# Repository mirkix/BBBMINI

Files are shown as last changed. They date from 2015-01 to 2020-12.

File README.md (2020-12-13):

# BBBmini

BeagleBone Black / Green  (BBB / BBG) Linux ArduPilot DIY Cape

(https://youtu.be/SqyfN3FStvs)

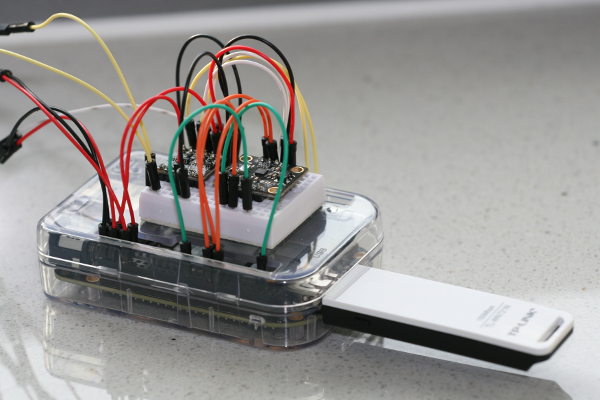
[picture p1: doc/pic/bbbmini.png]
BBBMINI breadboard


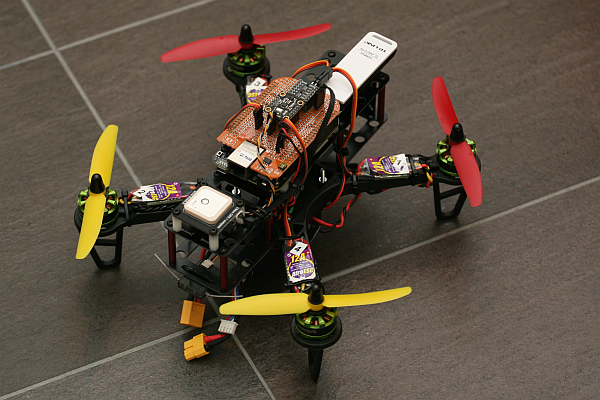
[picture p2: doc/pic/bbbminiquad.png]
BBBMINI Quad


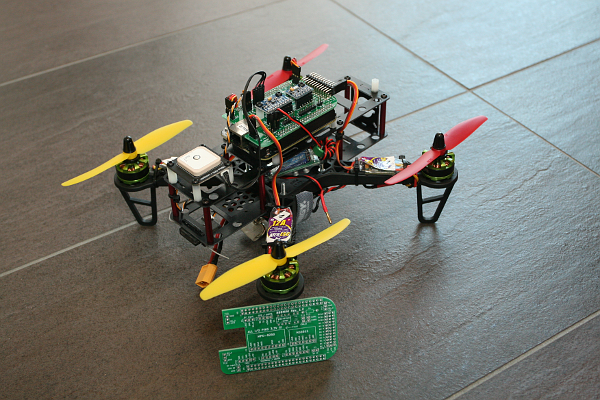
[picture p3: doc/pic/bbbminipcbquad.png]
BBBMINI Quad


# Why?
* Have fun to build your own BeagleBone ArduPilot Cape
* Easy start to ArduPilot Linux development
* No SMD soldering required
* DIY friendly connector

# About BBBmini
BBBmini is an autopilot / flightcontroller Cape for the BeagleBone. BBBmini + BeagleBone can be used as a state of the art Linux autopilot / flightcontroller for Copter, Planes or Rovers. BBBmini can be used with ArduPilot (open source unmanned aerial vehicle flight stack. BBBmini is a DIY project using widely available IMU and barometer breakout sensor boards, there is no SMD soldering necessary. The design is made that everybody can build a BBBmini by himself. In flight internet connection is done via WiFi link.

What does BBBmini offer:

* DIY state of the art UAV autopilot / flightcontroller
* Easy to build, no SMD soldering necessary
* Free hardware, free software
* Autopilot / flightcontroller software is running on Real-Time Linux
* DIY friendly connectors 0.1” pin header
* 12 x PWM out with individual frequency for each channel
* RC in connector for PPM, S.BUS or spektrum satellite input
* MPU-9250 IMU 9 x DOF
* MS5611 barometer
* HC-SR04 ultrasonic rangefinder
* GPS for full autonomous flights
* Voltage and current sensing
* I2C connector for Status display and additional sensors
* SPI connector for second redundant IMU
* UART connector for GPS
* UART connector for telemetry
* CAN connector with on board CAN bus transceiver
* USB connector used for WiFi, Laser rangefinder or cameras
* Excellent cost-performance ratio

The BBBmini project development includes:
* BBBmini documentation / how to
* BBBmini PCB design done with Kicad all sources free available on Github
* Device tree file for BBBmini hardware
* PRU firmware: 12 x PWM OUT with better than 1us accuracy, separate frequency for each channel. RC input capture with 5ns accuracy, can be used to capture PPM, S.BUS or spektrum satellite
* PRU firmware: HC-SR04 Ultrasonic Rangefinder device driver
* Commits to ArduPilot project to get BBBmini supported by ArduPilot
* Development of status display device driver for ArduPilot
* Add redundancy sensors via SPI / I2C or UART
* Lots of test flights and fine tuning in hardware and software to get a stable and reliable BeagleBone Green flightcontroller

# Why BeagleBone

Once I had the idea to develop a flightcontroller, I have examined on the market available computer for their suitability. The following criteria should be met by the computer being used.

First, the computer should be very well supported by the community. As a result, a Raspberry Pi or BeagleBone could be used. In addition, the flightcontroller should be set up with as little as possible external components.

The decision was made for the BeagleBone. With the Programmable Real-Time Units of the BeagleBone, it is possible to create the BBBmini with only a few sensor breakout boards. In addition the BeagleBone offers many interfaces such as UART, SPI, I2C, CAN, USB and ADC. All these interfaces are used by the BBBmini.

## BeagleBone parts used for BBBmini

* Main CPU running Linux
* PRU0 device driver for HC-SR04 ultrasonic rangefinder
* PRU1 to generate 12 PWM signals and receive PPM, S.BUS or spektrum satellite input
* Grove / I2C for communication to the status display, external compass or Laser rangefinder
* GROVE / serial 2 for sensors like Laser Rangefinder
* Serial 4 for telemetry radio
* Serial 5 for GPS
* ADC for voltage and current sensing
* SPI1 for high speed data transfer from IMU and Baro sensor
* SPI0 for high speed data transfer from second redundant IMU or other hardware
* CAN for communication with ESCs and additional hardware
* USB for WiFi and camera connection for life HD video transmission
* Ethernet for communication on ground

# [Hardware](doc/hardware/hardware.md)
* [BeagleBone Black](https://beagleboard.org/black) or [BeagleBone Green](https://beagleboard.org/green)
* [BBBMINI-PCB](https://github.com/mirkix/BBBMINI-PCB) (recommended) or BeagleBone Proto Cape with IMU MPU-9250 breakout board and Baro MS5611 breakout board (try to get a GY-9250 and GY-63 breakout board)
* RC receiver (S.BUS, PPM-Sum, Spektrum Satellit SPM 9645)
* optional GPS receiver
* optional HC-SR04 Ultrasonic Module

Click [here](doc/hardware/hardware.md) for further instruction how to assemble the board.

# [Software](doc/software/software.md)
For instructions how to get, build, test and run the software click [here](doc/software/software.md).

# Hackster.io
Please check also my [BBBmini project description on hackster.io](https://www.hackster.io/mirkix/flying-beaglebone-green-448b60).

# Support

## Support Chat



## Forum

[ArduPilot Forum](http://discuss.ardupilot.org/c/hardware-discussion/linux-autopilots)

## User Group

[diydrones.com BBBmini User Group](http://diydrones.com/group/bbbmini)

# License

<br /><span xmlns:dct="http://purl.org/dc/terms/" property="dct:title">BBBmini</span> by <a xmlns:cc="http://creativecommons.org/ns#" href="https://github.com/mirkix" property="cc:attributionName" rel="cc:attributionURL">Mirko Denecke</a> is licensed under a <a rel="license" href="http://creativecommons.org/licenses/by-sa/4.0/">Creative Commons Attribution-ShareAlike 4.0 International License</a>.

UNLESS OTHERWISE MUTUALLY AGREED TO BY THE PARTIES IN WRITING, LICENSOR OFFERS THE WORK AS-IS AND MAKES NO REPRESENTATIONS OR WARRANTIES OF ANY KIND CONCERNING THE WORK, EXPRESS, IMPLIED, STATUTORY OR OTHERWISE, INCLUDING, WITHOUT LIMITATION, WARRANTIES OF TITLE, MERCHANTABILITY, FITNESS FOR A PARTICULAR PURPOSE, NONINFRINGEMENT, OR THE ABSENCE OF LATENT OR OTHER DEFECTS, ACCURACY, OR THE PRESENCE OF ABSENCE OF ERRORS, WHETHER OR NOT DISCOVERABLE. SOME JURISDICTIONS DO NOT ALLOW THE EXCLUSION OF IMPLIED WARRANTIES, SO SUCH EXCLUSION MAY NOT APPLY TO YOU. EXCEPT TO THE EXTENT REQUIRED BY APPLICABLE LAW, IN NO EVENT WILL LICENSOR BE LIABLE TO YOU ON ANY LEGAL THEORY FOR ANY SPECIAL, INCIDENTAL, CONSEQUENTIAL, PUNITIVE OR EXEMPLARY DAMAGES ARISING OUT OF THIS LICENSE OR THE USE OF THE WORK, EVEN IF LICENSOR HAS BEEN ADVISED OF THE POSSIBILITY OF SUCH DAMAGES.

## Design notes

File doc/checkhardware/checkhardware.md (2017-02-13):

# Check hardware
If your board is ready you can check that everything is working as expected.

To build the example code / test code follow the instructions below.

## Compile example / test code native on BeagleBone
1. `cd ardupilot`
2. `git checkout master`
3. `git submodule update --init --recursive`
4. `./waf configure --board=bbbmini`
5. `./waf examples` (take some time)
6. `cp build/bbbmini/examples/* /home/debian/`

## Cross compile example / test code (faster) with Ubuntu computer

1. `cd ardupilot`
2. `git checkout master`
3. `git submodule update --init --recursive`
4. `./waf configure --board=bbbmini`
5. `./waf examples`
6. `scp build/bbbmini/examples/* debian@beaglebone:/home/debian/`

## Check IMU
`sudo /home/debian/INS_generic`

## Check baro
`sudo /home/debian/BARO_generic`

## Check GPS
`sudo /home/debian/GPS_AUTO_test -B /dev/ttyO5`

## Check rcinput
`sudo /home/debian/RCInput`

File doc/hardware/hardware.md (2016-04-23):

#Hardware

## Schematic
Schematic

## PCB
PCB

## Assemble BBBmini

### Step 1: Solder resistor R4 and R5.

For 3.3V RC input signal use R4 = 0Ω (bridge) and R5 = open (see picture)

For 5V RC input signal use R4 = 1kΩ and R5 = 2kΩ

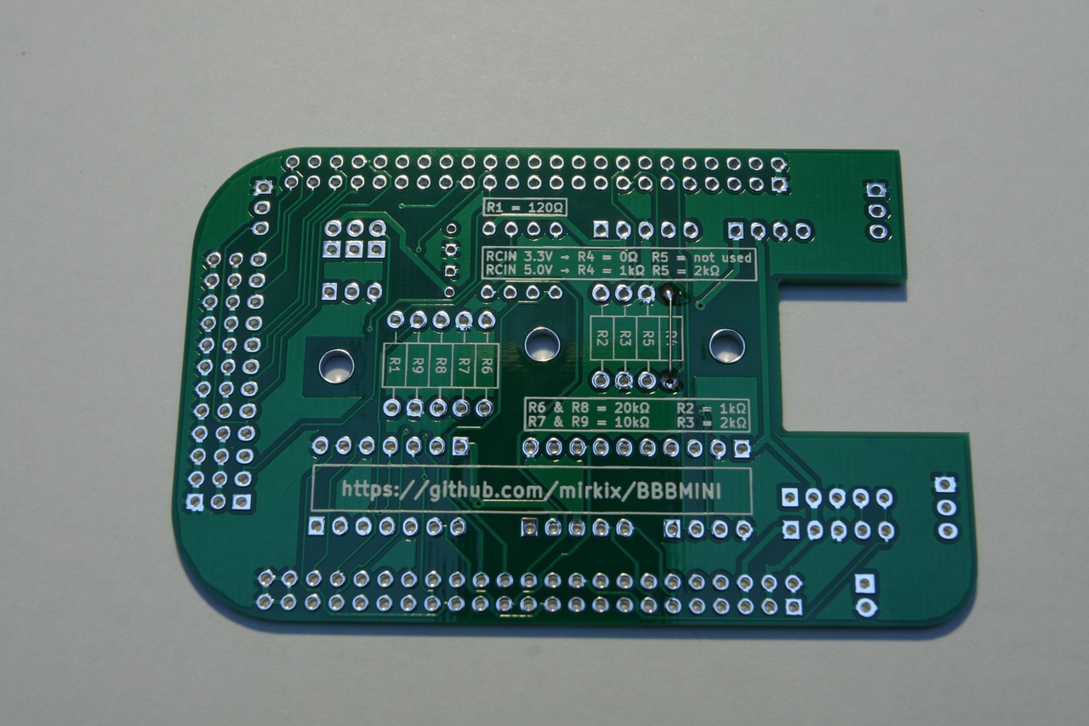
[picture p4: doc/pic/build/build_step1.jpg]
Solder R4 and R5


### Step 2:

Solder resistor

R1 = 120Ω

R2 = 1kΩ

R3 = 2kΩ

R6 = 20kΩ 0.1%

R7 = 10kΩ 0.1%

R8 = 20kΩ 0.1%

R9 = 10kΩ 0.1%

to the bottom layer. 

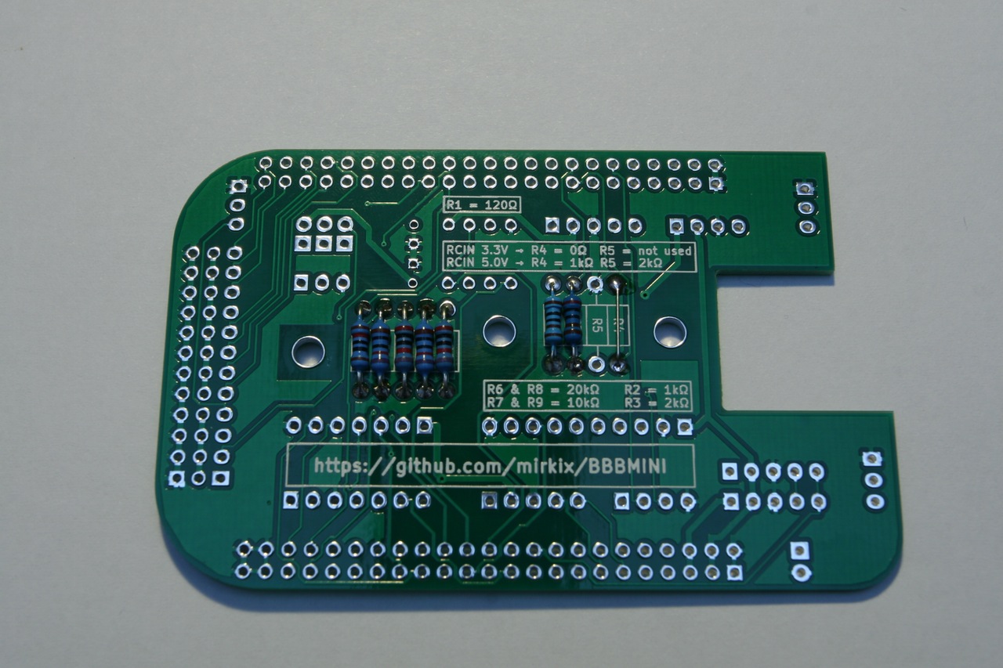
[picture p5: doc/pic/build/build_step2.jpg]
Solder R1, R2, R3, R6, R7, R8 and R9


### Step 3:

Solder CAN transceiver on the top layer

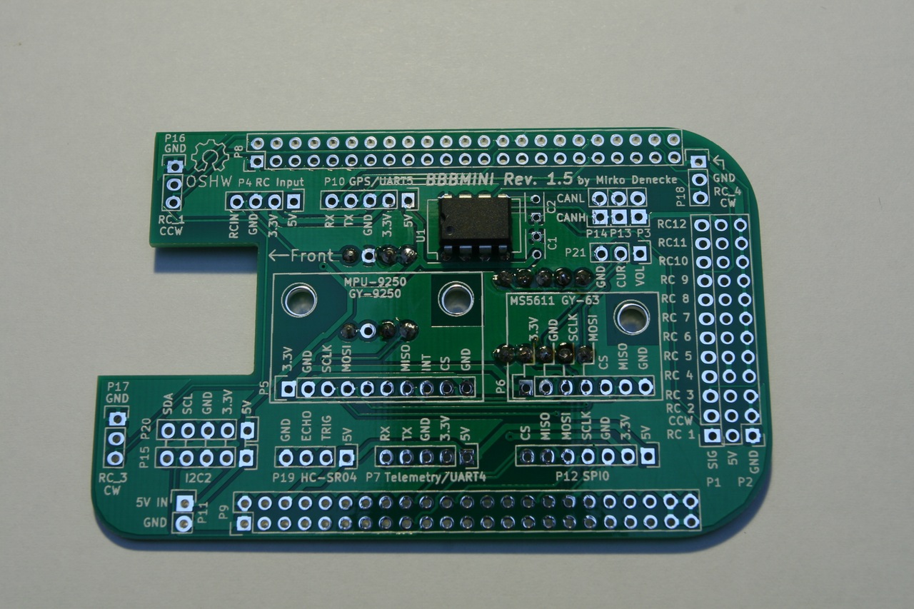
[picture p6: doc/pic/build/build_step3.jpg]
Solder CAN transceiver


### Step 4:

Solder male pin-header on top layer

P1, P2, P3, P4, P7, P10, P11, P12, P13, P14, P15, P16, P17, P18, P19, P20, P21

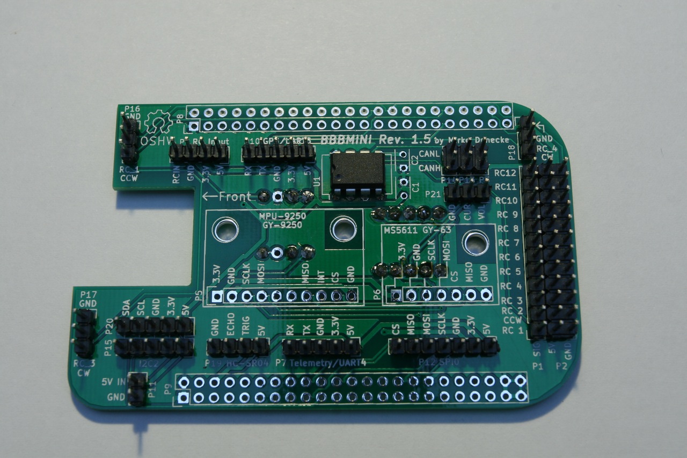
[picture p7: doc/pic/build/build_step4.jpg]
Solder P1, P2, P3, P4, P7, P10, P11, P12, P13, P14, P15, P16, P17, P18, P19, P20, P21


### Step 5:

Solder C1 and C2

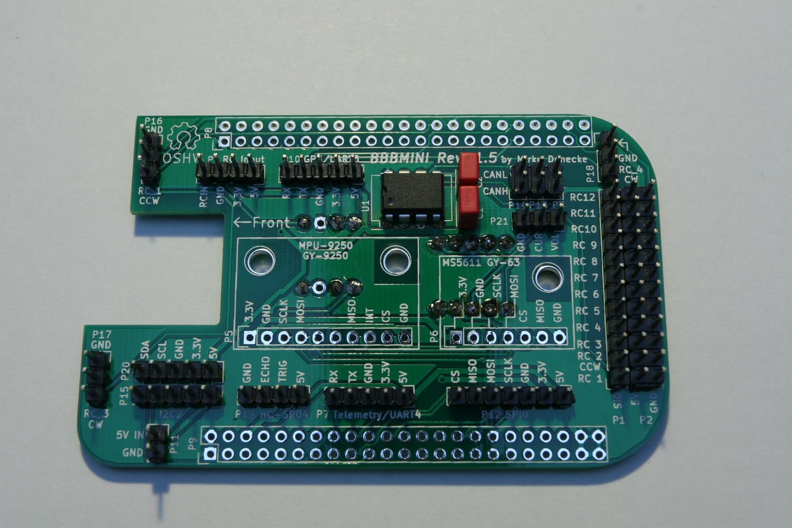
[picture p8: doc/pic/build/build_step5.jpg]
Solder C1 and C2


### Step 6:

Solder female pin-header P5 and P6 on top layer

Solder P5 and P6

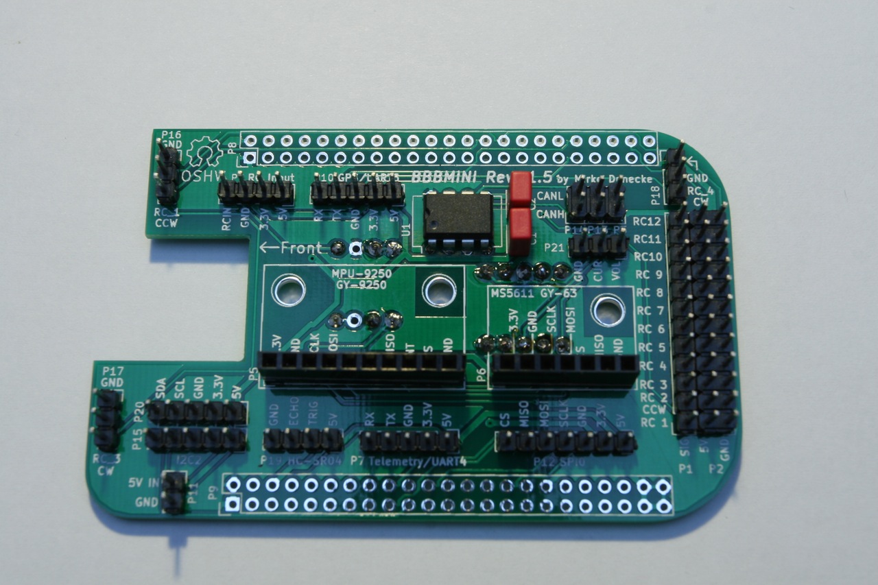
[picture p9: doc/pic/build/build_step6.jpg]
Solder P5 and P6


### Step 7:

Solder male pin-header P8 and P9 to bottom layer

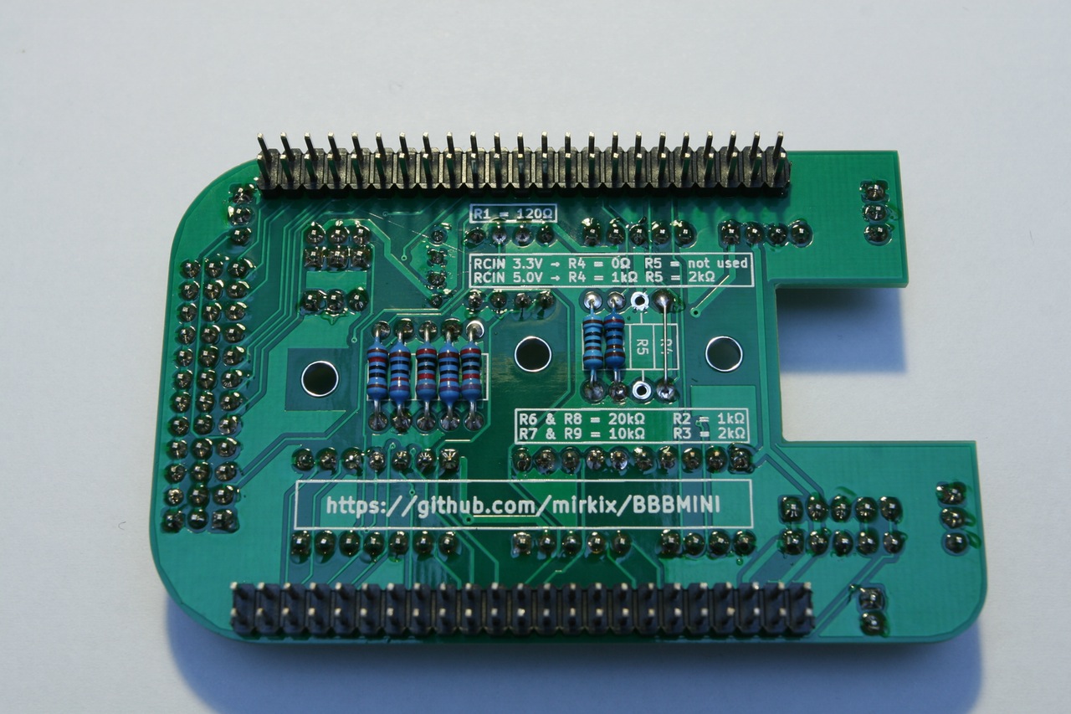
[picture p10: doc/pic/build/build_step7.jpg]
Solder P8 and P9


### Step 8:

Solder male pin-header to bottom layer of GY-9250 and GY-63

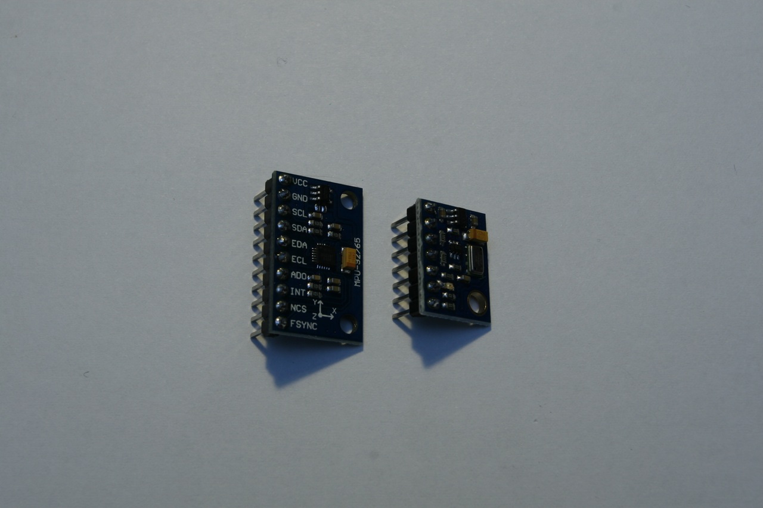
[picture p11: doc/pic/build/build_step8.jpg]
Solder pin-header for GY-9250 and GY-63


### Step 9:

Mount spacer to BBBmini

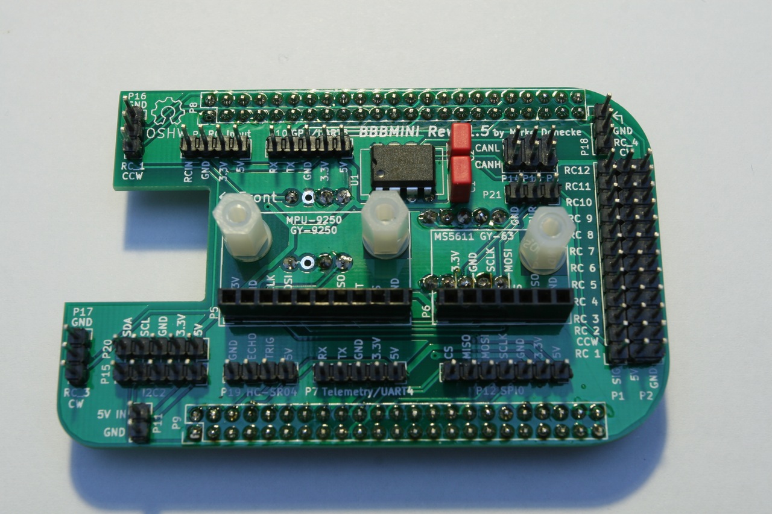
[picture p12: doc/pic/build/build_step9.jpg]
Mount spacer


### Step 10:

Mount GY-9250 and GY-63

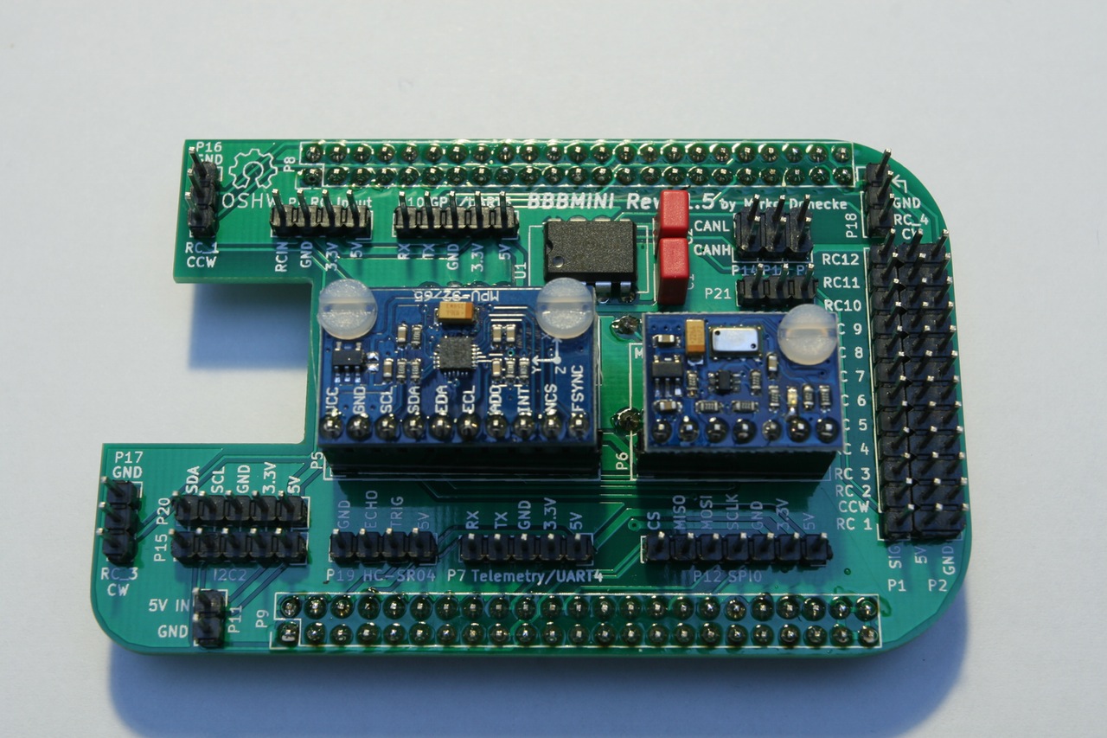
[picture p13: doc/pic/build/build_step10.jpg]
Mount GY-9250 and GY-63


### Finish! BBBmini is ready to use for Copter, Planes or Rover.

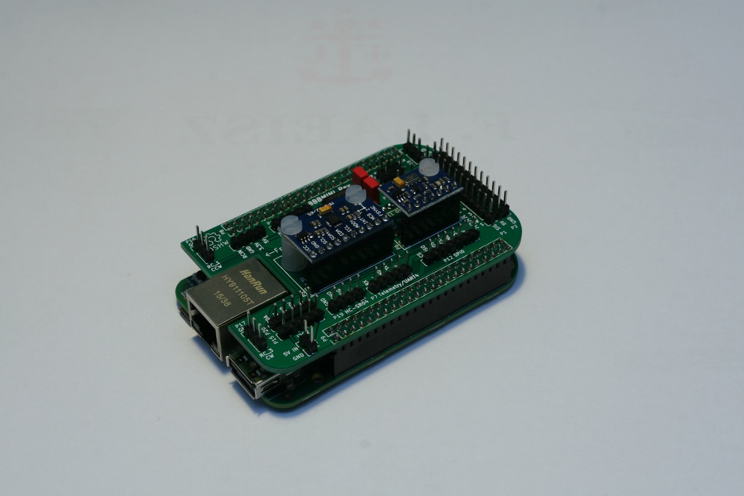
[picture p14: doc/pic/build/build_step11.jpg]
BBBmini


## Connect BBBmini

### Connect motors and ESC
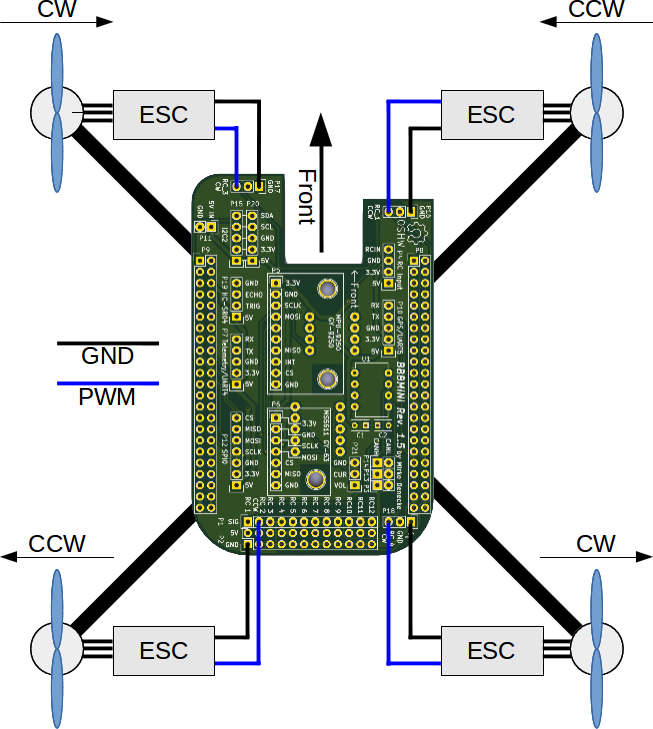
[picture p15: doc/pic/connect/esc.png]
Connect motors and ESC


### Connect power distribution

* Connect each ESC to the power distribution board
* Connect the 5V power distribution board output to BBBmini P11 power input
* Connect the voltage and current sensing power distribution board output to BBBmini P21 voltage and current sensing pins

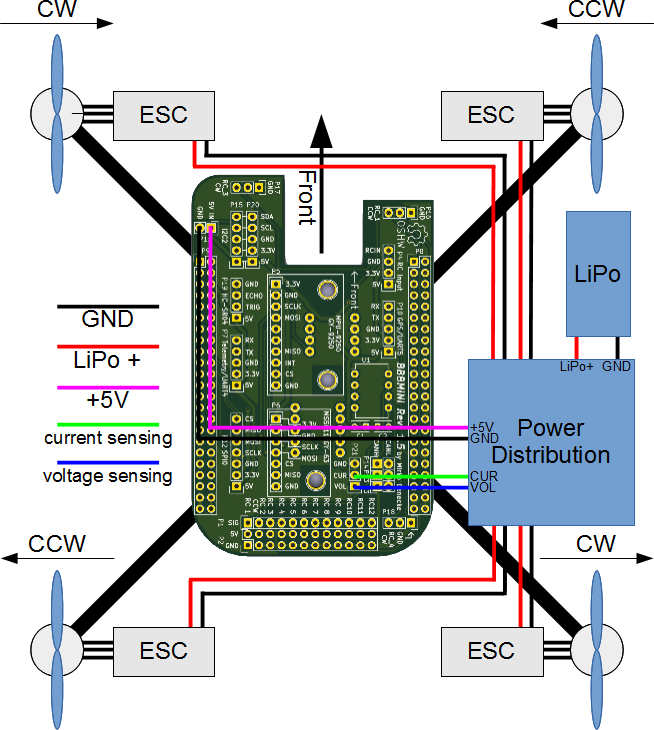
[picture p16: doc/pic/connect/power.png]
Connect power distribution


### Connect RC receiver
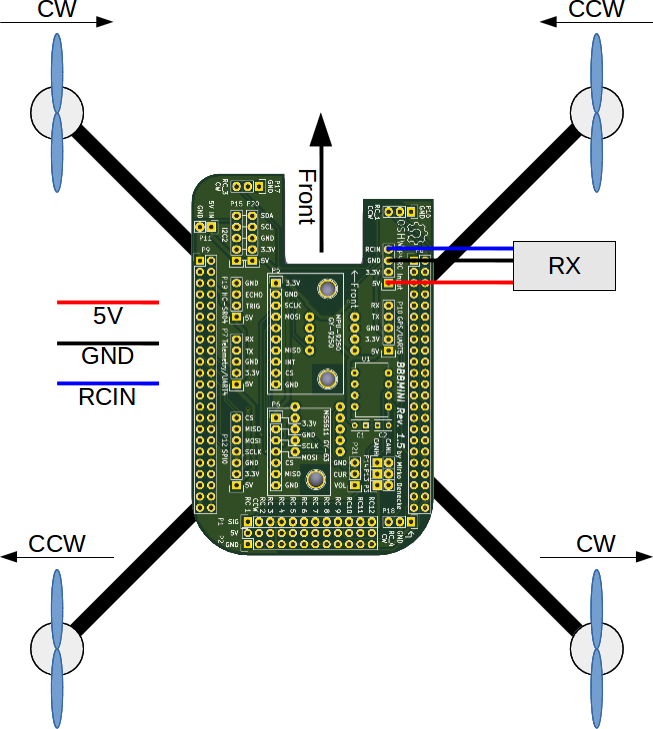
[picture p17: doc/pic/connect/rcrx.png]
Connect RC receiver


### Connect display
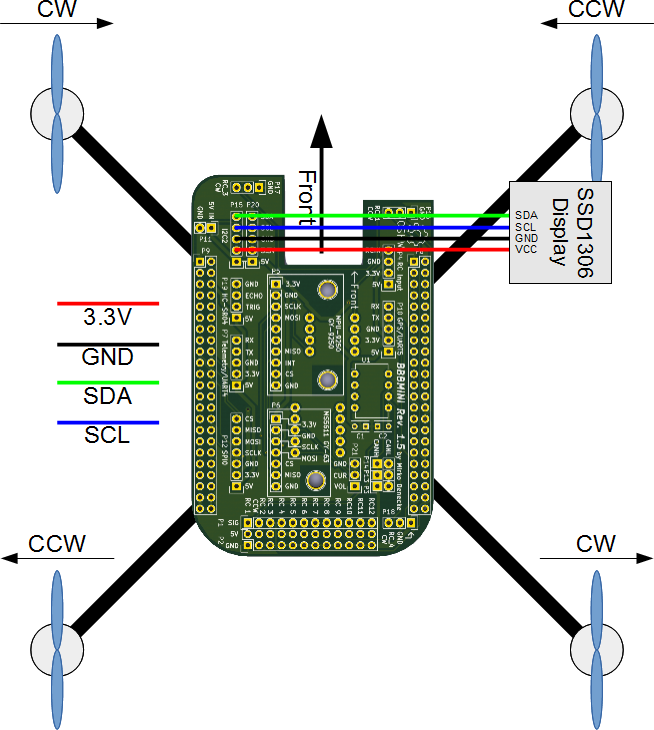
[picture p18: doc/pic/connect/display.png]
Connect display


### Connect GPS

* Connect your GPS to P10.
* P10 +3.3V to GPS VCC
* P10 GND to GPS GND
* P10 RX to GPS TX
* P10 TX to GPS RX

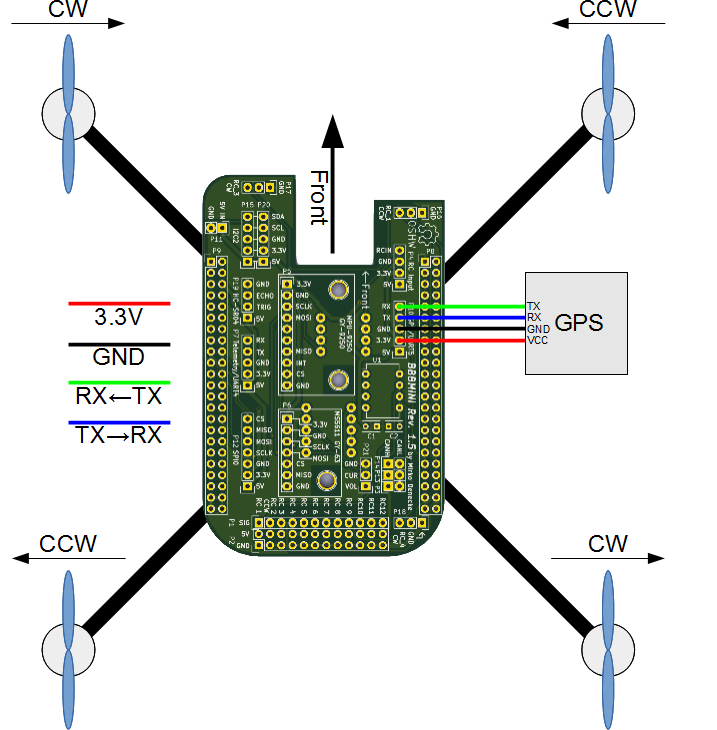
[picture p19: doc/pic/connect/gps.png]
Connect GPS


### Connect telemetry

* Connect your telemetry radio to P7.
* P7 +5V to telemetry radio VCC
* P7 GND to telemetry radio GND
* P7 RX to telemetry radio TX
* P7 TX to telemetry radio RX

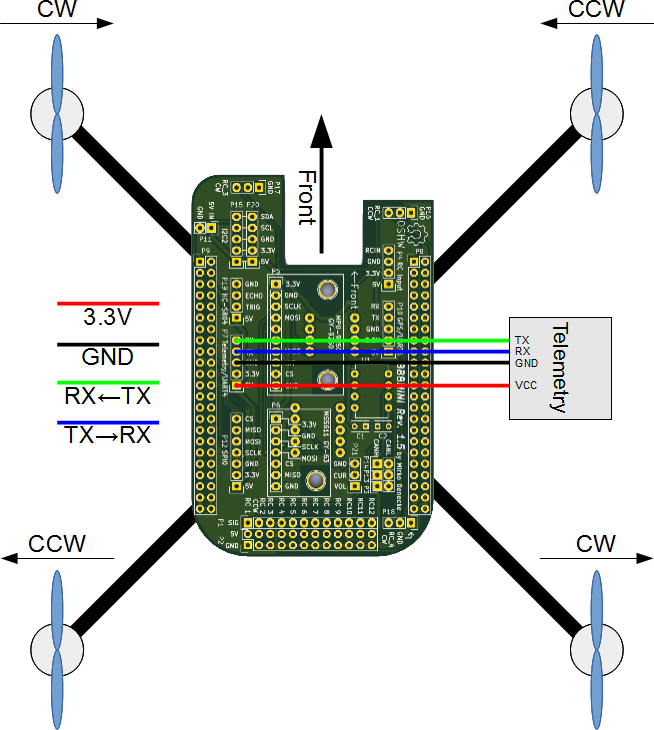
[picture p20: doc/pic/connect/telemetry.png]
Connect telemetry


### Connect HC-SR04

* Connect your HC-SR04 ultrasonic rangefinder
* P19 +5V to HC-SR04 VCC
* P19 GND to HC-SR04 GND
* P19 TRIG to HC-SR04 TRIG
* P19 ECHO to ECHO TRIG

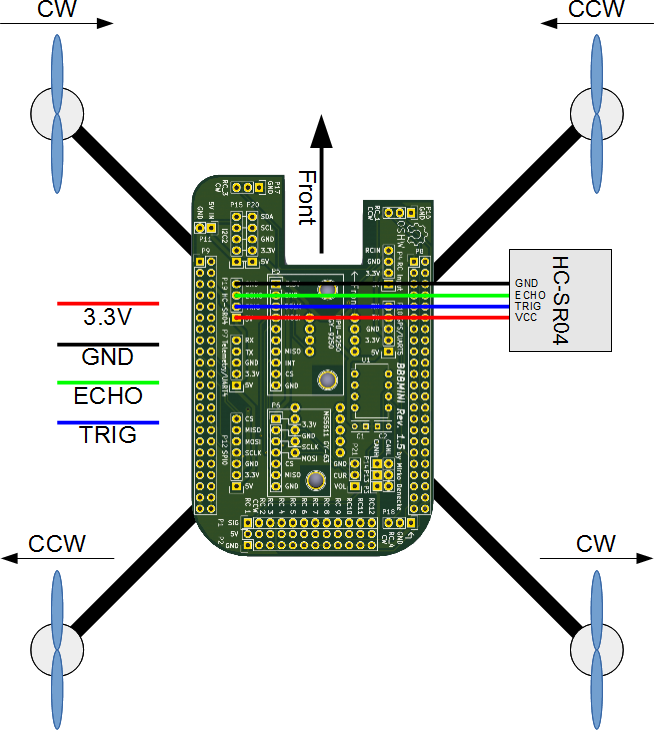
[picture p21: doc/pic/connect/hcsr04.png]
Connect HC-SR04


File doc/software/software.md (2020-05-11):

# Software

How to prepare your BeagleBone to use as BBBmini.

* Debian 8.6 jessie
* GCC 4.9
* Kernel 4.4 PREEMPT RT
* BBBmini devicetree loaded at startup.

## Prepare microSD with your Linux host computer
1. Download Debian image [https://rcn-ee.net/rootfs/bb.org/testing/2016-10-02/console/BBB-blank-debian-8.6-console-armhf-2016-10-02-2gb.img.xz](https://rcn-ee.net/rootfs/bb.org/testing/2016-10-02/console/BBB-blank-debian-8.6-console-armhf-2016-10-02-2gb.img.xz)
2. Decompress image: `unxz BBB-blank-debian-8.6-console-armhf-2016-10-02-2gb.img.xz`
3. Use `lsblk` to find the address `/dev/sdX` of your microSD device, such as `/dev/sdc`. `/dev/sdX` should point to your microSD device, not partition, be careful here to make sure you don't wipe the wrong device or partition!!! Unplug your microSD card and run lsblk again then plug it back in, if you want to verify it's the correct device.
4. Copy image to microSD card (>= 2GB), the process can take 15-30 minutes depending on the speed of your microSD card: `sudo dd bs=4M if=./BBB-blank-debian-8.6-console-armhf-2016-10-02-2gb.img of=/dev/sdX status=progress`
5. `sync` and remove microSD 

## Install Debian to your BeagleBone eMMC
1. Plug prepared microSD into BeagleBone
2. While holding down the boot button, apply power to the board. If there is a newer Debian installed, holding down the boot button is not necessary.
3. Wait some minutes until Debian is installed (all four LEDs turned on).
4. Remove power.
5. Remove microSD.
6. Apply power again.
7. Connect to the BeagleBone `ssh debian@beaglebone`
8. Password `temppwd`
9. Update software: `sudo apt update && sudo apt upgrade -y`
10. Install software: `sudo apt install -y bb-cape-overlays cpufrequtils g++ pkg-config gawk git make screen python python-dev python-lxml python-pip python-future`
11. Set link to pkg-config: `sudo ln -s pkg-config /usr/bin/arm-linux-gnueabihf-pkg-config`
12. Update scripts: `cd /opt/scripts && sudo git pull`
13. Expend partition: `sudo /opt/scripts/tools/grow_partition.sh`
14. Install RT Kernel: `sudo /opt/scripts/tools/update_kernel.sh --bone-rt-kernel --lts-4_4`
15. Add BBBmini DTB: `sudo sed -i 's/#dtb=$/dtb=am335x-boneblack-bbbmini.dtb/' /boot/uEnv.txt`
16. Add ADC DTBO: `sudo sed -i 's/#cape_enable=bone_capemgr.enable_partno=/cape_enable=bone_capemgr.enable_partno=BB-ADC/g' /boot/uEnv.txt`
17. Set clock to fixed 1GHz `sudo sed -i 's/GOVERNOR="ondemand"/GOVERNOR="performance"/g' /etc/init.d/cpufrequtils`
18. Reboot system: `sudo reboot`
19. Login again: `ssh debian@beaglebone`
20. Your BeagleBone is now ready to use.

## Compile ArduPilot native on BeagleBone
1. `cd ~`
2. `git clone https://github.com/ardupilot/ardupilot.git`
3. `cd ardupilot`
4.  * for ArduCopter `git checkout Copter-3.6.7`
    * for ArduPlane `git checkout ArduPlane-3.9.6` or `git checkout ArduPlane-beta` 
    * for ArduRover `git checkout Rover-3.5.0`
    * for ArduSub `git checkout ArduSub-stable` or `git checkout ArduSub-beta`
5. `git submodule update --init --recursive`
6. `./waf configure --board=bbbmini`
7. `./waf` (take about 1h20m)
8. `cp build/bbbmini/bin/* /home/debian/`

## Cross compile ArduPilot (faster) with Ubuntu computer

Get the source code:

1. `cd ~`
2. `git clone https://github.com/ardupilot/ardupilot.git`
3. `cd ardupilot`
4. `./Tools/scripts/install-prereqs-ubuntu.sh`
5.  * for ArduCopter `git checkout Copter-3.6.7`
    * for ArduPlane `git checkout ArduPlane-3.9.6` or `git checkout ArduPlane-beta` 
    * for ArduRover `git checkout Rover-3.5.0`
    * for ArduSub `git checkout ArduSub-stable` or `git checkout ArduSub-beta`
6. `git submodule update --init --recursive`
7. `./waf configure --board=bbbmini`
8. `./waf`
9. `scp build/bbbmini/bin/* debian@beaglebone:/home/debian/`

## Run ArduPilot
Now you can check your hardware [here.](../checkhardware/checkhardware.md)

ArduCopter:
`sudo /home/debian/arducopter` (plus parameter) 

ArduPlane:
`sudo /home/debian/arduplane` (plus parameter) 

ArduRover:
`sudo /home/debian/ardurover` (plus parameter) 

ArduSub:
`sudo /home/debian/ardusub` (plus parameter) 

Parameter mapping:

start parameter | ArduPilot serial port 
------------ | -------------
-A | SERIAL0
-B | SERIAL3
-C | SERIAL1
-D | SERIAL2
-E | SERIAL4
-F | SERIAL5

Check http://ardupilot.org/copter/docs/parameters.html#serial0-baud-serial0-baud-rate to set the right value for `SERIALx_BAUD` and `SERIALx_PROTOCOL`

To connect a MAVLink groundstation with IP 192.168.178.26 add `-C udp:192.168.178.26:14550`

To use MAVLink via radio connected to UART4 add `-C /dev/ttyO4`. 

If there is a GPS connected to UART5 add `-B /dev/ttyO5`. 

Example: MAVLink groundstation with IP 192.168.178.26 on port 14550 and GPS connected to `/dev/ttyO5` UART5.

`sudo /home/debian/arducopter -C udp:192.168.178.26:14550 -B /dev/ttyO5`

Example: MAVLink groundstation via radio connected to UART4 and GPS connected to `/dev/ttyO5` UART5.

`sudo /home/debian/arducopter -B /dev/ttyO5 -C /dev/ttyO4`

## Automatic start ArduPilot after boot

If ArduPilot should start automatically at boot time follow the instructions below:

1. Connect to your BeagleBone via ssh with `ssh debian@beaglebone`
2. Edit `/etc/rc.local` with `sudo nano /etc/rc.local`
3. Modify file to (use your ArduPilot file and parameter):
```
#!/bin/sh -e
#
# rc.local
#
# This script is executed at the end of each multiuser runlevel.
# Make sure that the script will "exit 0" on success or any other
# value on error.
#
# In order to enable or disable this script just change the execution
# bits.
#
# By default this script does nothing.

/bin/sleep 10
/home/debian/arducopter -B /dev/ttyO5 -C /dev/ttyO4 > /home/debian/arducopter.log &

exit 0
```
4. Save file: `Strg + o` + Enter
5. Exit nano: `Strg + x`
6. Reboot BegaleBone with `sudo reboot`

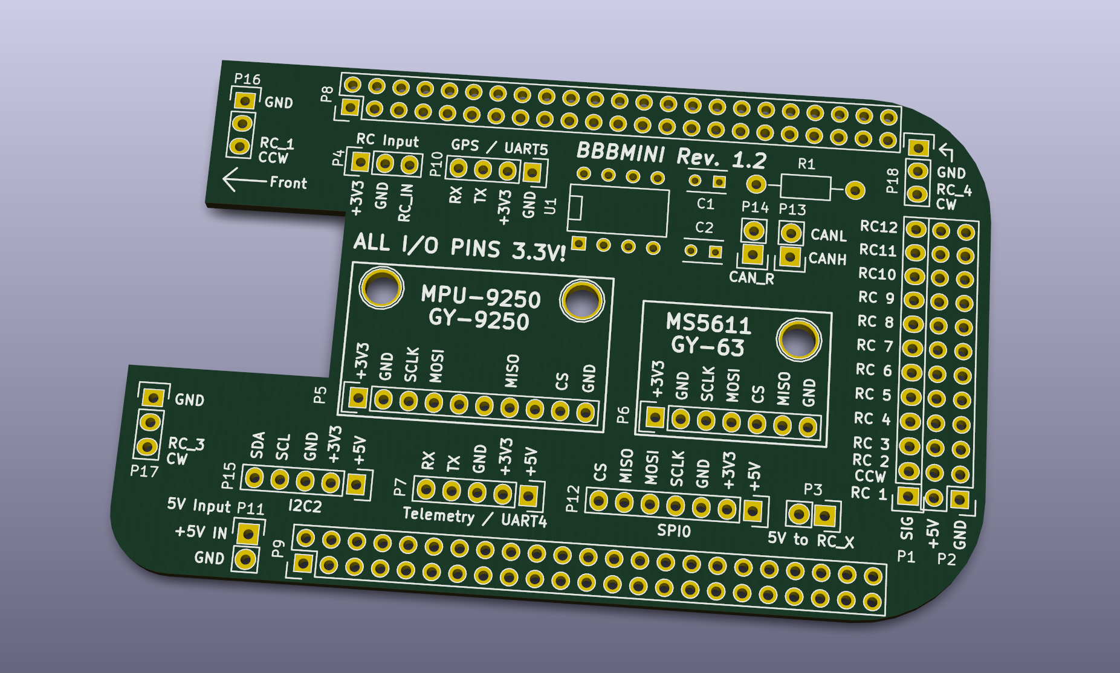
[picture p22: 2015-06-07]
doc/pic/pcb.png

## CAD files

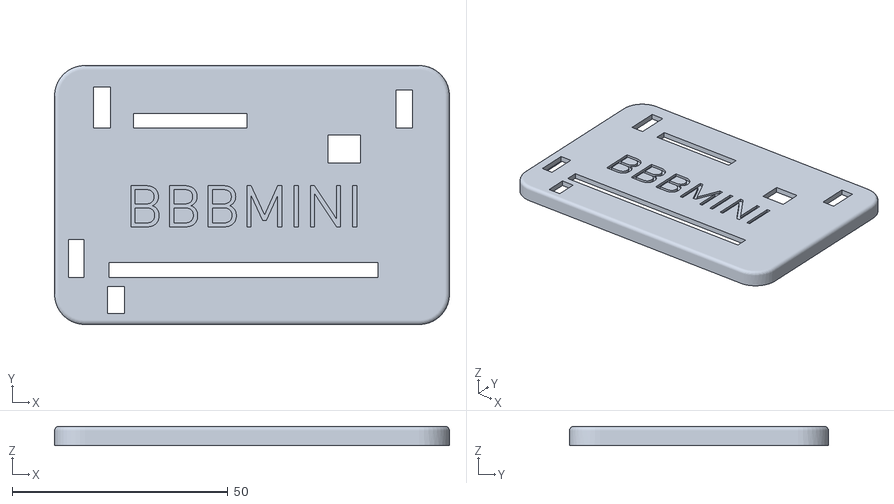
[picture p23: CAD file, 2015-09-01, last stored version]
bbbmini_1_4_top_typo.stl
91.5 x 60.0 x 4.46

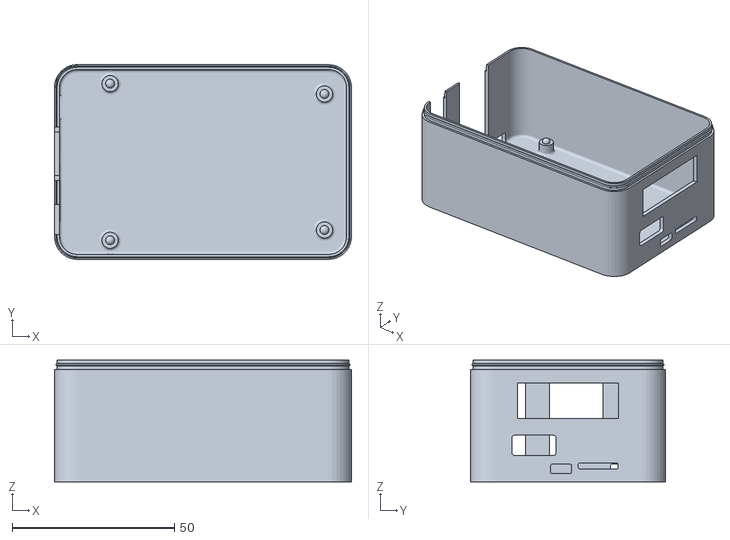
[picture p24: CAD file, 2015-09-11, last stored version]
case/bbbmini_1_4_case_lifted.stl
91.5 x 60.0 x 37.5

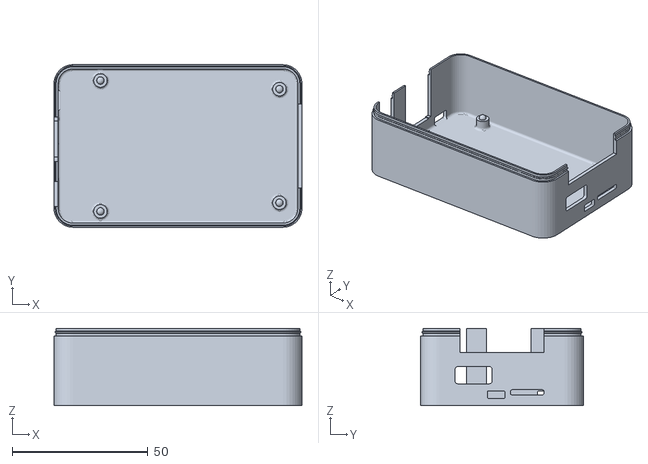
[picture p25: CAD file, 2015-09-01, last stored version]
case/bbbmini_1_4_case.stl
91.5 x 60.0 x 28.5

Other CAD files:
bbbmini_1_4_top_blank.stl
case/bbbmini_1_4_top_blank.stl

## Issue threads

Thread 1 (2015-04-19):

Clarification

awright424, 2015-04-19:
Can you provide higher resolution pictures of the front and the back of your cape? how are you powering the beaglebone black? Is it being powered by a esc?

mirkix, 2015-04-20:
The BBB(MINI) is powered by a UBEC 5V / 3A which is connected to the SYS_5V pins (P9.07 and P9.08) [Power supply](https://github.com/mirkix/BBBMINI/blob/master/doc/hardware/hardware.md). High resolutions pictures will follow.

awright424, 2015-04-22:
Is the use of a logic level converter necessary? I have so far a cape with a mpu9250 soldered properly and am waiting for my ms5611. from there I just need to know what else would be necessary. I already have a logic level converter as well.

mirkix, 2015-04-23:
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

mirkix, 2015-04-23:
The four ESCs are connected without logic level converter. The GPS is connected with logic level converter, but it can changed to 3.3 Volt I/O also. You should not connect 5 Volt signals to BBB inputs.

awright424, 2015-04-25:
So I got my ms5611 in today and soldered it up. So I now have the mpu9250 and the ms5611. However I can not get ardupilot to detect both correctly. With them both connected Ardupilot automatically fails. With only the mpu9250 it fails on detecting the barometer. running the imu tests in the libraries\AP_IntertialSensor\examples it fails to detect the mpu9250 with both connected and reports a bad crc error for the ms5611. What could be causing this?

mirkix, 2015-04-25:
You have to connected the ms5611 even if you start the AP_IntertialSensor example. Could you post the console output, when you start the example.

awright424, 2015-04-25:
Here is my output when running the test with both modules connected:
ubuntu@arm:~/ardupilot/libraries/AP_InertialSensor/examples/INS_generic$
sudo ./INS_generic.elf
AP_InertialSensor startup...
Failed to boot MPU9250 5 times
Failed to boot MPU9250 5 times
Failed to boot MPU9250 5 times
Failed to boot MPU9250 5 times
Failed to boot MPU9250 5 times
Failed to boot MPU9250 5 times
No INS backends available
Failed to boot MPU9250 5 times

If I disconnect pin 29 on the ms5611 it detects the mpu9250.

starting ardupilot gives me this output with all pins connected minus p9.29
for the ms5611:

./ArduCopter.elf

Init APM:Copter V3.3-dev (5f8c05b7)

Free RAM: 4096
FW Ver: 120
----------------------------------------

load_all took 132us
0 0 0 �     Q  }��      Q  ���3   � Calibrating barometerz�PANIC:
AP_Baro::read unsuccessful for more than 500ms in AP_Baro::calibrate [2]

root@arm:/home/ubuntu/ardupilot/ArduCopter# ./ArduCopter.elf

Init APM:Copter V3.3-dev (5f8c05b7)

Free RAM: 4096
FW Ver: 120
----------------------------------------

Bad CRC on MS5611
load_all took 128us

the bad crc on MS5611 has me wondering if the chip is the culprit.

On Sat, Apr 25, 2015 at 7:16 AM, Mirko Denecke <notifications@github.com>
wrote:

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

mirkix, 2015-04-25:
Does the INS_generic run (the hole test) without problems when the p9.29 is not connected? Do you check the chip select lines (MS5611 P9.42 and MPU-9250 P9.28)? Can you post a picture of your board please.

awright424, 2015-04-25:
With p9.29 disconnected and other pins still connected to the ms5611 does
not interfere with the mpu9250. I can run the INS_generic and calibrate and
test the mpu9250. with p9.29 connected it fails to boot the mpu9250.

AP_InertialSensor startup...
Failed to boot MPU9250 5 times
Failed to boot MPU9250 5 times
Failed to boot MPU9250 5 times
Failed to boot MPU9250 5 times
Failed to boot MPU9250 5 times
Failed to boot MPU9250 5 times
No INS backends available
Failed to boot MPU9250 5 times

On Sat, Apr 25, 2015 at 9:16 AM, Mirko Denecke <notifications@github.com>
wrote:

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

mirkix, 2015-04-25:
I just tested the version (5f8c05b7) that you also used, everything works fine on my side. May some wires are wrong. Which kind a breakout boards do you use?

awright424, 2015-04-25:
http://www.ebay.com/itm/251637098006?_trksid=p2057872.m2749.l2649&ssPageName=STRK%3AMEBIDX%3AIT
ms5611

http://www.ebay.com/itm/381029304894?_trksid=p2057872.m2749.l2649&ssPageName=STRK%3AMEBIDX%3AIT
mpu9250

these are the modules i purchased

On Sat, Apr 25, 2015 at 10:34 AM, Alex Wright <alexomarwright@gmail.com>
wrote:

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

mirkix, 2015-04-25:
MS5611
Did you connect:
PS to low
SCL to P9.31
CSB to P9.42
SDO to P9.29
SDA to P9.30

awright424, 2015-04-25:
The only thing not connected is ps to low. would that just need to be
connected to ground?

On Sat, Apr 25, 2015 at 4:34 PM, Mirko Denecke <notifications@github.com>
wrote:

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

mirkix, 2015-04-25:
Yes, that set the communication mode to SPI, otherwise it is I2C.

awright424, 2015-04-25:
that took care of the issue. ArduCopter says that im ready to fly. I'll
solder up my servo/esc connections and start testing the other portions of
this build

On Sat, Apr 25, 2015 at 4:45 PM, Mirko Denecke <notifications@github.com>
wrote:

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

awright424, 2015-04-26:
I've got to bother you with another question. I was wondering If I have this mpu9250 oriented properly?

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

mirkix, 2015-04-27:
I have to look, but you can change it by modifying: https://github.com/diydrones/ardupilot/blob/master/libraries/AP_InertialSensor/AP_InertialSensor_MPU9250.cpp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

mirkix, 2015-04-27:
If you use the unmodified SP_InertialSensor_MPU9250.cpp file, the pin 1 dot of the MPU-9250 has to point to the left and to the tail of the copter.
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

awright424, 2015-04-27:
From what you are saying, and with me assuming that vcc is pin 1 then with the way I have things soldered up I would need to either have the ethernet port side of the beaglebone black facing the left of the craft. If necessary I have no problem desoldering the breakouts from the protocape to orient better and possible even lay items out in a more concise manner.
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

mirkix, 2015-04-27:
Do you already connect your board to a ground station software via Ethernet? There you can check if the orientation fits. If it not right you could change it in software as described earlier. I add the orientation to the documentation yet.

awright424, 2015-04-27:
No ground control station yet. Couldnt find anything in the gentoo repo's.
Will probably install something on my odroid u3 that is running ubuntu to
use in conjunction with the beaglebone black. Will probably try to get that
going when I get home from work later.

On Mon, Apr 27, 2015 at 3:53 PM, Mirko Denecke <notifications@github.com>
wrote:

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

awright424, 2015-05-07:
I switched the orientation of the module after getting it hooked up to mission planner and seeing that it was indeed soldered incorrectly. This is good to go now on my part. I will be getting the power for the beaglebone black and servos situated now.

Closed 2015-05-07.

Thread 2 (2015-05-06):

Powering servos and other 5v to 3v items?

awright424, 2015-05-06:
I specifically will be taking my first flight in gas plane and will need to operate at least 4 servos. These are futaba fp-s148 servos. I see that they can operate between 5v and 6v. How would you recommend routing power? I understand you plan on powering the beaglebone black itself through a 5v ubec would you also use this source and just connect the servos to it as well? I know with a quadcopter this is not so much of an issue as you only need to provide ground and signal to the escs.

mirkix, 2015-05-06:
I would recommend to use a second ubec.

awright424, 2015-05-08:
what other hardware will be supported under BBBMINI? Will a buzzer and a way to check voltage be supported?

mirkix, 2015-05-10:
A buzzer could be connected to pin P8.36, but you have to use a power amplifier, because it is a 3.3V low current output. Voltage monitoring is not supported at the moment.

awright424, 2015-05-11:
So are you saying a logic level converter would be necessary for the buzzer?

mirkix, 2015-05-11:
I think a logic level converter will not work here. You have to convert the 3.3V PWM signal into a signal which can driver your buzzer. The necessary part depends on your buzzer.

Closed 2015-06-10.

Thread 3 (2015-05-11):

overlays pru loaded for bbbmini

awright424, 2015-05-11:
I have been looking at the startup.sh located in the bbbmini directory for the device tree's. I have noticed that unlike the pxf or the startup.sh located under linux_hal_essentials that it does not initialize the pru. So at this point I am lost. with the startup.sh under the bbbmini the pru isnt initialized nor is the firmware loaded for them.

mirkix, 2015-05-11:
The PRU will be initialized within this file https://github.com/diydrones/ardupilot/blob/master/Tools/Linux_HAL_Essentials/devicetree/bbbmini/BB-BBBMINI-00A0.dts (https://github.com/diydrones/ardupilot/blob/master/Tools/Linux_HAL_Essentials/devicetree/bbbmini/BB-BBBMINI-00A0.dts). The firmware for PRU is loaded here https://github.com/diydrones/ardupilot/blob/master/libraries/AP_HAL_Linux/RCOutput_AioPRU.cpp#L56.

Run startup.sh to initialize the PRU, the firmware is loaded at runtime.

BBBMINI uses only one PRU for RC input and RC output. So all should work and is already tested.

awright424, 2015-05-11:
The reason I ask is I noticed when running the startup.sh loaded in the root of the ardupilot/Tools/Linux_HAL_Essentials it mentions the fact that the pru is initialized. looking at the dts for the bbbmini I dont see anywhere where the pru firmware is loaded or referenced. I do not see the pru being intialized when loading the bbbmini overlay as well.

awright424, 2015-05-14:
I also have another question about the kernel u=you used during flight. I know a kernel with preempt or rt preempt is needed from my reading. I could not find any .debs or anything for a kernel that the erlerobot project was using. Can you shed some light on the kernel and the dtbo as the rc output isnt working for me. I tried changing servo parameters through mavlink and saw no change.

mirkix, 2015-05-14:
I used this to compile the RT Kernel: http://dev.ardupilot.com/wiki/building-the-code/building-for-beaglebone-black-on-linux/. Did you try the example sketch for RC OUT https://github.com/diydrones/ardupilot/tree/master/libraries/AP_HAL/examples/RCOutput ? This is a good point to start debugging.

mirkix, 2015-05-14:
The first dmesg show that you load the BBBMINI device tree (at 399 s) and then also load the pxf device tree (at 1011 s) you should only load the BBBMINI device tree!
The 'make: pasm: Command not found' shows that the assembler is not installed on your system. But that is not necessary anyway. The PRU firmware is already build  (https://github.com/diydrones/ardupilot/blob/master/Tools/Linux_HAL_Essentials/pru/aiopru/RcAioPRU_bin.h).

awright424, 2015-05-14:
I have loaded the bbbmini overlay after rebooting and still saw issues in dmesg related to the pru. I am in the process of building the RCoutput example to see if that can shed light on things.

http://pastebin.com/HQ99jb4s  <-- dmesg after loading the overlay.

[  335.303516] omap_hwmod: pruss: failed to hardreset
^ the above line leads me to believe the pru is not being setup correctly. especially after doing some research on the error.

mirkix, 2015-05-14:
this is my dmesg output:

http://pastebin.com/rB3ygHcr

there is also the pruss: failed to hardreset, but that seems to not be a problem.

awright424, 2015-05-14:
hmmm, thats interesting. I tried running the RCOutput.elf not sure if it needed any parameter to be run with or if it needed to be built any differently. Makefile didn't show any options.

mirkix, 2015-05-14:
to build the test sketch you should use `make bbbmini`

the output should look like this:
```
mirko@arm:~/bin$ sudo ./RCOutput.elf
Starting AP_HAL::RCOutput test
reversing
reversing
reversing
reversing
reversing
^Cmirko@arm:~/bin$
```

awright424, 2015-05-14:
I built the aiopru firmware and copied it over to /lib/firmware. I also rebuilt the RCOutput and now get the proper output. I will be home in an hour or two and can then verify that the servos are or are not working. Does this application test all servo outputs?

awright424, 2015-05-14:
I made it home and hooked up my servos to my servo outputs and got nothing. I can hear the servo being powered on but get no movement from the servos.

mirkix, 2015-05-22:
Is the console output like:
```
Starting AP_HAL::RCOutput test
reversing
reversing
```

Maybe the 3.3 Volt signal is to low. I tested the rc output with servos without any problems.

awright424, 2015-05-22:
These are servos I have been able to get working with pwm pins before without using any sort of logic level converter so I dont believe that is the issue. I will more than likely just load the overlay remove the cape and connect signal directly to one of the rc outputs to see if that makes any difference.

mirkix, 2015-05-22:
Could you post the result from `cat /sys/devices/bone_capemgr.9/slots`.

It should look like this:
```
0: 54:PF---
 1: 55:PF---
 2: 56:PF---
 3: 57:PF---
 4: ff:P-O-L Bone-LT-eMMC-2G,00A0,Texas Instrument,BB-BONE-EMMC-2G
 5: ff:P-O-- Bone-Black-HDMI,00A0,Texas Instrument,BB-BONELT-HDMI
 6: ff:P-O-- Bone-Black-HDMIN,00A0,Texas Instrument,BB-BONELT-HDMIN
 7: ff:P-O-L Override Board Name,00A0,Override Manuf,BB-BBBMINI
 8: ff:P-O-L Override Board Name,00A0,Override Manuf,am33xx_pwm
 9: ff:P-O-L Override Board Name,00A0,Override Manuf,bone_pwm_P8_36
```

mirkix, 2015-06-03:
There is now a prebuild Debain 8 image with 4.0.4 PREEMPT RT Kernel, GCC 4.9 and device tree already installed. It is not necessary to load any device tree files. Maybe you give it a try. https://github.com/mirkix/BBBMINI/blob/master/doc/software/software.md

awright424, 2015-06-04:
Yes I can test that today when I have a chance. Anyway you would be able to send me one of those spiffy pcb's you added?

awright424, 2015-06-04:
Oh and rcnee may have added your dts file due to me asking questions in #beagle

mirkix, 2015-06-04:
Yes sure, I can send you a Rev 1.0 pcs. Unfortunately there is one pin swap in the layout, but when you know that, it should not be a problem. Just send me your address to mirkix@gmail.com. There will be a Rev 1.1 without the pin swap and cleaner layout soon.

Closed 2015-06-10.

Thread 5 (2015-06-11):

Latest image

awright424, 2015-06-11:
I dd'ed the latest image to a microsd card and rebuilt everything. Now when I try to run any of the test programs or even try to start arducopter.

I get this error:
debian@arm:~/ardupilot/ArduCopter$ sudo ./ArduCopter.elf
RCOutputAioPRU.cpp:SIGBUS error gernerated

Any ideas?
And if you needed me to provide postage for the pcb let me know. I am eagerly awaiting to try it out. it looks tons better than my birdnest.

awright424, 2015-06-12:
I am no longer receiving this error. Should have realized this was due to me updating to the latest kernel as i needed the kernel source to be able to build a wireless module that was necessary.

Closed 2015-06-12.

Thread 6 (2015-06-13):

RC_out issues

aaraujo11, 2015-06-13:
Hi @mirkix ,

First of all congratulations for this project, nice work!!!

So i'm trying it with a different platform, i'm using a hexarotor. And so far i successfully got working the IMU MPU9250, Baro MS5611, the GPS Neo-m8 ublox. For the receiver i'm using an FRsky X8R connected to RC_in in the define BBB pins. The FRsky X8R operate with SBUS protocol, it is tested and working. I have also tested the RC_out, and all 6 motors are operating correctly. For last i had configure the APM planner to communicate with the BBB using wireless network.

Basically the issue is, after launch ArduCopter.elf,  when i try to throttle or send other commands in the radio, the motors don't respond to any of them. In the APM planner i can see in the "Radio Calibration" section, the radio commands work fine (roll, throttle, pitch, yaw) as well in the "FailSafe" section in "Radio In" column. But in the "Motor Out" column the corresponding outputs bars remain static. Do you have any clue of the problem is? (or as I have recently start to explore the Ardupilot code, probably could be any configuration i'm missing)

mirkix, 2015-06-13:
Hi @aaraujo11 ,
it sounds a little bit to me, that you did not arm the ArduCopter. Can you check that please. http://copter.ardupilot.com/wiki/flying-arducopter/arming_the_motors/

aaraujo11, 2015-06-17:
Hi @mirkix,

Yeah... "Arm the motors by holding the throttle down, and rudder right for 5 seconds." :laughing: simply a noob at APM.  Thanks. Solved!

Closed 2015-06-17.

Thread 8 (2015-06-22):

kernel source, gstreamer with ardupilot.

awright424, 2015-06-22:
I was wondering if there was anyway you would be able to provide the kernel source/headers as a .deb? I need to build wifi drivers for my 80211ac adapter.

I have also recently built gstreamer 1.4.5 on my beaglebone black and have been playing around with streaming. Have you had any experience with this and do you think the beaglebone could handle this and ardupilot? I am using a logitech c920 so the camera does all the grunt of video encoding.

http://docs.emlid.com/Navio-APM/video-streaming/
I was able to stream video to my android phone using the apk provided here. Might be interesting to use this application in conjunction with google cardboard or modified for cardboard for fpv.

Also if you have not mailed the pcb I can pay to have it expedited as I would love to get my hands on it.

mirkix, 2015-06-22:
Hi Alex,

unfortunately I did not create a .deb until now. Maybe you can give me some instructions how to build the .deb, then I will try it.

The Kernel was build with the `bb-kernel`GitHub project from RobertCNelson. For further instruction look at https://eewiki.net/display/linuxonarm/BeagleBone+Black#BeagleBoneBlack-LinuxKernel .

The video-streaming sound very interesting, but I have not made any video-streaming with a BBB. But keep us informed, it would be a nice feature.

I mailed the PCB one or two weeks ago, but the German postal goes on strike just here. I also send some PCBs to other people in Germany, they do not arrived there also until now.

Best regards
Mirko

khancyr, 2015-06-25:
Hi ,

If you use bb-kernel , to create .deb, you can use
``` ./build_deb.sh
```
instead of
``` ./build_kernel.sh
```

awright424, 2015-06-25:
Mirko,
 Other than hoping the kernel has the ability for me to just zcat /proc/config.gz to get the config was there anything else you did in order to make things work for the pru etc? I dont mind compiling the kernel if necessary. Should be able to build on an x86_64 host with the arm compilers. I know its easier done through a debian based system.

mirkix, 2015-06-28:
Thanks for the information about the `./build_deb.sh`thinks can be so easy. RobertCNelson now also provide a RT-PREEMPT image for the BeagleBone Black. You can install it with `sudo apt-get install linux-image-4.0.6-bone-rt-r5`. With r6 there will be BBBMINI device tree support by the kernel out of the box. That should make thinks much more easier and the BBBMINI image is not necessary any more. The device tree for the BBBMINI is now merged into https://github.com/RobertCNelson/dtb-rebuilder.

awright424, 2015-06-28:
so I installed the version specified and received errors on starting ardupilot:

RCOutputAioPRU.cpp:SIGBUS error gernerated

mirkix, 2015-06-29:
The device tree is not included in the r5 kernel. So you have to do:
```
git clone https://github.com/RobertCNelson/dtb-rebuilder.git
cd dtb-rebuilder
make clean
make
make install
```
after that you have to add `dtb=am335x-boneblack-bbbmini.dtb` behind `uname_r=4.0.6-bone-rt-r5` in the file `uEnv.txt` than reboot. `uEnv.txt` is located under `/boot`if you are using Debian.

awright424, 2015-06-30:
Thanks that did the trick. I also received the 2 pcb's you sent. ordering another mpu9250 and ms5611 to make sure i didn't damage the boards when desoldering them. I have noticed some device errors, that go away away after reboot.

Thanks again for sending the pcb's I know you said there was something I needed to know when it came to the pcb's themselves. You said some wiring needed to be switched?

mirkix, 2015-06-30:
Yes, right. With PCB Rev 1.0 boards you should NOT use P11 to power the cape and the beagle bone. To power the beagle bone and the cape use +5V pins from P15 or P7 or P12. You can also power the beagle bone and the cape via the power plug of the beagle bone. This is fixed with the Rev 1.2 boards. You should also not close jumper P3.

mirkix, 2015-06-30:
There is now the 4.0.6-bone-rt-r6 kernel available form Robert C Nelson. In this kernel the `am335x-boneblack-bbbmini.dtb`device tree file is already included. You only have to add it to the uEnv.txt file (`dtb=am335x-boneblack-bbbmini.dtb`). `dtb-rebuilder`is not necessary anymore.

mirkix, 2015-07-10:
Hi Alex,

you can use Rev1.0 boards with limitations:

- Do not power the board via P11 use instead +5V pin from P15, P7, P12 to
power the board. Or you can also power the board and bbb via the power plug
of the bbb.
- Please do not close P3
- The Quad-Frame extra RC-Outputs are at the wrong corners

All these things are fixes with Rev1.2.

There is now also a Rev1.4 available (https://github.com/mirkix/BBBMINI-PCB).
I add a level shifter to the RC_IN so you can plug a 5V RX direct to the
bbbmini and also add a Port to connect a HC-SR04 a 2$ (aliexpress) Ultra
Sonic Rangefinder (range 3cm to 400cm, with 1cm accuracy).

Best regards Mirko

2015-06-30 15:56 GMT+02:00 awright424 <notifications@github.com>:

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

mirkix, 2015-07-10:
Sorry answer this twice.

2015-07-10 10:35 GMT+02:00 Mirko Denecke <mirkix@googlemail.com>:

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

awright424, 2015-07-20:
This can be closed. I was wondering though if you could send me one of the latest pcb's if you have anymore. I am at the point of choosing a receiver and transmitter combo to go with my 9xr pro and would love one of the latest pcb's. If you have paypal let me know I can definitely provide postage plus a tip for your work and help.

Closed 2015-07-21.

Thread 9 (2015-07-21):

Software .dtb

awright424, 2015-07-21:
Can you add a section to the software area that deals with building the pru firmware and loading the proper overlay with the 4.0 kernel. I have updated my kernel from your image but seem to be having issues with the overlay loading and the pru's working.

mirkix, 2015-07-26:
Hi Alex,
it is not necessary to build the PRU firmware. If you are using Kernel 4.0 you have to do:
`git clone https://github.com/RobertCNelson/dtb-rebuilder.git`
`cd dtb-rebuilder`
`git checkout 4.0.x`
`make clean`
`make`
`sudo make install`

After that you have to modify the `/boot/uEnv.txt` file.

`sudo nano /boot/uEnv.txt`

Add a line:
`dtb=am335x-boneblack-bbbmini.dtb`

Now reboot.

awright424, 2015-07-26:
Thank you will try that out. Is there any chance of me being able to get
the latest revision of the pcb? I will probably try to get something 3d
printed as to not damage the cape and the beaglebone black.
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

mirkix, 2015-07-26:
I Alex,
the Rev 1.4 boards unfortunately not arrived here until now. I will inform you when they are available.  You can also produce your own batch, take a look on this description:
https://github.com/mirkix/BBBMINI-PCB#pcb

awright424, 2015-08-02:
I finally took a deeper look. the bbbmini is not included the dtb-builder repo it is included the bb-overlays repo. Now I am wondering if I should be cloning that repo and attempting to load the cape versus the dtb. will report back.

mirkix, 2015-08-02:
Hi Alex,

it is in the `dtb-rebuilder` repo as I have written above. https://github.com/RobertCNelson/dtb-rebuilder/blob/4.0.x/src/arm/am335x-boneblack-bbbmini.dts

awright424, 2015-08-02:
it is only available in the 4.0.x branch so cloning and building will not get you the dtb

Closed 2015-08-05.

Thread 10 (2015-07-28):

Segment fault

juvinski, 2015-07-28:
Hi,

I'm trying to run Arducopter following the BBB Mini software, but if I try to run any test software or arducopter I'm receiving this segment fault

(gdb) run
Starting program: /home/debian/ardupilot/libraries/AP_InertialSensor/examples/INS_generic/INS_generic.elf
[Thread debugging using libthread_db enabled]
Using host libthread_db library "/lib/arm-linux-gnueabihf/libthread_db.so.1".

Program received signal SIGSEGV, Segmentation fault.
0x000140e2 in Linux::LinuxI2CDriver::LinuxI2CDriver (this=0x33690 <i2cDriver0>, semaphore=<optimized out>, device=<optimized out>)
    at /home/debian/ardupilot/libraries/AP_HAL_Linux/I2CDriver.cpp:36
36	        hal.scheduler->panic("I2C device is not a chardev node");

Any clue ?

Regards

mirkix, 2015-07-29:
Hi,
check if there is a `/dev/i2c-2` device  (`ls /dev/*i2*`).
Best regards
Mirko

juvinski, 2015-07-29:
Hi,
thanks for your reply.
Yes there is two devices on i2c
ls /dev/*i2*
/dev/i2c-0  /dev/i2c-1

I remove the board and wihtout nothing connected still get this error. Btw, i2cdetect comman has output reading i2cbus
i2cdetect -r 0
WARNING! This program can confuse your I2C bus, cause data loss and worse!
I will probe file /dev/i2c-0 using read byte commands.
I will probe address range 0x03-0x77.
Continue? [Y/n] y
     0  1  2  3  4  5  6  7  8  9  a  b  c  d  e  f
00:          -- -- -- -- -- -- -- -- -- -- -- -- --
10: -- -- -- -- -- -- -- -- -- -- -- -- -- -- -- --
20: -- -- -- -- UU -- -- -- -- -- -- -- -- -- -- --
30: -- -- -- -- 34 -- -- -- -- -- -- -- -- -- -- --
40: -- -- -- -- -- -- -- -- -- -- -- -- -- -- -- --
50: 50 -- -- -- -- -- -- -- -- -- -- -- -- -- -- --
60: -- -- -- -- -- -- -- -- -- -- -- -- -- -- -- --

i2cdetect -r 1
WARNING! This program can confuse your I2C bus, cause data loss and worse!
I will probe file /dev/i2c-1 using read byte commands.
I will probe address range 0x03-0x77.
Continue? [Y/n] y
     0  1  2  3  4  5  6  7  8  9  a  b  c  d  e  f
00:          -- -- -- -- -- -- -- -- -- -- -- -- --
10: -- -- -- -- -- -- -- -- -- -- -- -- -- -- -- --
20: -- -- -- -- -- -- -- -- -- -- -- -- -- -- -- --
30: -- -- -- -- -- -- -- -- -- -- -- -- -- -- -- --
40: -- -- -- -- -- -- -- -- -- -- -- -- -- -- -- --
50: -- -- -- -- UU UU UU UU -- -- -- -- -- -- -- --
60: -- -- -- -- -- -- -- -- 68 -- -- -- -- -- -- --
70: -- -- -- -- -- -- -- 77

thanks

awright424, 2015-07-29:
Any ideas on this? Or is there a revision that doesnt exhibit this behavior that I can checkout? I was hoping to begin testing and tuning later on today.

juvinski, 2015-07-29:
Hi awright424,

are you with same problem ?

awright424, 2015-07-29:
https://github.com/diydrones/ardupilot/issues/2616

Here is what I have so far and I also have the i2c devices. This issue popped up within the last week or two as I have been thinking it was a dtb issue on my end.

awright424, 2015-07-30:
Any ideas on what is causing this? I have not been able to get off the ground due to this one issue.

juvinski, 2015-07-30:
Hi awright424,

first thing I'm doing is compiling a new kernel and trying debian and ubuntu images to check if the problem is on linux/kernel or ardupilot code, what beaglebone are you using? I'm using beaglebone black revision A6

awright424, 2015-07-30:
juvinski,
 I have a revision C beaglebone black. I dont believe compiling a new kernel will be necessary. I will attempt to use ubuntu myself and then compile the bbbmini overlay/dtb and try to load it at boot. I believe the firmware for the pru needs to be in /lib/firmware I will double check that.

I do not have my serial cable so I will not be able to debug the boot if something goes wrong.

mirkix, 2015-07-30:
Hi,

you need a `/dev/i2c-2` device entry. This is the i2c bus the BBBMINI use.

mirkix, 2015-07-30:
Are you using Debian? And which version / Kernel?

juvinski, 2015-07-30:
Hi Mirko,

I'm using a GY-87 (http://www.goodluckbuy.com/gy-87-10dof-mpu6050-hmc5883l-bmp180-three-axis-gyroscopeacceleratormagnetic-field.html) on i2-c bus.
Debian 8 and 7 sd cards was used and with same problem.
I tryed use Arducopter too(compiling using make linux) and the problem (segment fault) are happening too, this is why I'm suspecting something on linux layer(kernek 3.8.13 bone 70)

mirkix, 2015-07-30:
Hi,

can you try this image please https://github.com/mirkix/BBBMINI/blob/master/doc/software/software.md , that should work.

juvinski, 2015-07-30:
Hi Mario.
That was me first try :(

awright424, 2015-07-30:
That's the image I am using as well.

mirkix, 2015-07-30:
I will check that tomorrow, maybe I have to update the image.

awright424, 2015-07-30:
I have followed your instructions mriko about building the dtb for the
bbbmini and booting with it but that does not work as I have a device that
does not boot using the 4.2 kernel at that point. If you could provide
instructions on building and placing firmware etc for the beaglebone black
then an image would not be necessary but welcomed none the less.

On Thu, Jul 30, 2015 at 4:49 PM, Mirko Denecke <notifications@github.com>
wrote:

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

juvinski, 2015-07-31:
Hi,

I was looking the Arducopter code and I think maybe I have a clue.
On my beaglebone I´m with ic2 devices 0 and 1 but Arducopter code for BBBMINI is looking for a i2c device 2 as follow

static LinuxSemaphore  i2cSemaphore0;
static LinuxI2CDriver  i2cDriver0(&i2cSemaphore0, "/dev/i2c-2");

I will try to change this address tomorow and see what will happen.

Regards

awright424, 2015-07-31:
https://github.com/diydrones/ardupilot/blob/master/libraries/AP_HAL_Linux/HAL_Linux_Class.cpp

looking at this file it looks like they were attempting to add both i2c devices? from what i can ascertain I believe it should look like this for the bbbmini.

#elif CONFIG_HAL_BOARD_SUBTYPE == HAL_BOARD_SUBTYPE_LINUX_BBBMINI
static LinuxSemaphore  i2cSemaphore0;
static LinuxI2CDriver  i2cDriver0(&i2cSemaphore0, "/dev/i2c-0");
#else
static LinuxSemaphore  i2cSemaphore1;
static LinuxI2CDriver  i2cDriver0(&i2cSemaphore1, "/dev/i2c-1");
#endif
static LinuxSPIDeviceManager spiDeviceManager;

juvinski, 2015-07-31:
Hi,
what i2c devices you have?
what is the return of ls /dev/i2* command?

awright424, 2015-07-31:
ls /dev/i2c-*
/dev/i2c-0  /dev/i2c-1

juvinski, 2015-07-31:
You can try to change to i2c-1 or 0 compile and try to run?

awright424, 2015-07-31:
yeah i changed it and am compiling to try and run now

awright424, 2015-07-31:
that seems to have fixed the issue. it compiled and started without segfaulting. going to check things out.

juvinski, 2015-07-31:
Nice.

I will do some tests and let you know about the results.

Regards - BTW - I received an email from shen2you and my boards will be shipped tomorow :)

awright424, 2015-07-31:
Are these 1.4 boards I could use one. I need to get a couple. wish it had voltage sensing capabilities as well.

juvinski, 2015-07-31:
What sensors are you using?

earsneyes, 2015-07-31:
Good job guys! I was suffering as well.
Just tested it with a Drotek 10DOF imu (MPU9250, MS5611).

juvinski, 2015-07-31:
Hi,

anyone has problems with ToneAlarm?
Init APM:Copter V3.3-rc8 (818ef282)

Free RAM: 4096
FW Ver: 120
----------------------------------------

load_all took 32us
ToneAlarm: Error!! please check if PWM overlays are loaded correctlyAP_Notify: Failed to initialise ToneAlarmBad CRC on MS5611

mirkix, 2015-07-31:
Thats is ok, bbbmini has no ToneAlarm. Maybe I will remove ToneAlarm for bbbmini, to avoid this message.

juvinski, 2015-07-31:
Hi Mirko,
There someway to avoid that ? My arducopter is not running :(

mirkix, 2015-07-31:
Hi,

just updated https://github.com/mirkix/BBBMINI/blob/master/doc/software/software.md#prepare-bbb . Please check that, it should fix your `/dev/i2c-2` things and enable the Range Finder support.

mirkix, 2015-07-31:
@juvinski
That is not the reason arducopter is not working. The reason is the `Bad CRC on MS5611`. There is no communication with the MS5611 baro sensor. Do you have a MS5611 connected to the SPI bus?

phoneguy, 2015-08-03:
Hi,
    I just tested out your latest image and i2c devices now working in Ardupilot.  Thanks!

Closed 2015-08-03.

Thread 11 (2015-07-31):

connecting rc receiver

awright424, 2015-07-31:
Mirko,
 I was looking at the pdf for the bbbmini schematic and noticed the resistors that were attached to rc input. Is this to act as a logic level shifter? How should i go about using connecting a receiver to  a 1.2 board?

mirkix, 2015-07-31:
Alex, it depends on which RC receiver do you use. If it is a 3.3Volt receiver, you can connect the output direct to the input of the Rev 1.2. If you are using a 5V RC receiver, you have to use a 5V to 3.3V level converter, or try something like in the Rev 1.4 (voltage divider).

Closed 2015-07-31.

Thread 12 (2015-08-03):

Receiver question

juvinski, 2015-08-03:
Hi All,

one question - it's not clear to me until now is about the receiver.
What kind of receiver can be used? PPM or PWM will work? On the board there are one RC_Input with Voltage Divider and another 3 inputs with X_Quad name and I couldn't figured out what is the purpose.

Regards

awright424, 2015-08-03:
Need one with ppm sum, cppm or sbus. I use a orangerx r620x connected to bind port

juvinski, 2015-08-03:
Hi,
This part for me is a little hard.
I have 2 turnigy receivers, 2 dsm2 and one openrls(http://www.hobbyking.com/hobbyking/store/__27096__OrangeRx_Open_LRS_433MHz_9Ch_Receiver.html)
One of this can work?
Thanks

earsneyes, 2015-08-04:
@juvinski PPM or SBUS should work. I successfully tested an Orange 7 Channel DSM2 and a FrySky X8R SBUS receiver.

The RC_1, RC_2 and RC_4 pins are the outputs needed for a quadcopter.
Only the RC input will work with the receiver so no PWM input.

Cheers

awright424, 2015-08-04:
If your receiver doesn't do ppm sbus you can get a ppm encoder. But a receiver that does sbus cppm or ppm will be better.

mirkix, 2015-08-04:
@juvinski
For a connector description look here: https://github.com/mirkix/BBBMINI-PCB#connector .

juvinski, 2015-08-04:
Hi Mirko,
great, now is more clear, except by one thing, P15, P16  and P17 are the motors output for X Quad, but they are for motors, 1, 3 and 4, and how about motor 2 ?

mirkix, 2015-08-04:
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

juvinski, 2015-08-04:
Sorry

Closed 2015-09-18.

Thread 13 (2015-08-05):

powering and sensing battery current and voltage.

awright424, 2015-08-05:
i have some questions. I have purchased this, http://www.ebay.com/itm/141729072661, power module to power my beaglebone black. I purchased it due to the fact that it does battery measurement and current sensing. Can this be made to be used with bbbmini?

mirkix, 2015-08-05:
I started a project two day ago. It is a small digispark module connected to the i2c port of the bbbmini. The digispark board is connected to the power module you have and will report voltage and current to the bbbmini. I think it will take about a month to get it working.

awright424, 2015-08-13:
cool. i got it in today and wouldnt mind testing that as well.

Closed 2015-08-13.

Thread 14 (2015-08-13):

Quadcopter flipping on take off

awright424, 2015-08-13:
I have gotten my quad together and the beaglebone black is working fine. I however have not been able to fly yet due to it flipping. I am not sure if I have something wired wrong with the motors but everything should be fine. If there is anything you can suggest that  would help. I will probably make a video to show whats happening.

juvinski, 2015-08-13:
Hi,
first of all, lets start from beginning. have you already made the ESC calibration and was ok ?

awright424, 2015-08-13:
I have manually calibrated esc's tried through the beaglebone as well, though I'm not sure it was done right

juvinski, 2015-08-13:
ok, what ESCs are you using ?
Do you know when can make the video ?

awright424, 2015-08-13:
Emax 12a simonk esc's. Should be able to make one in 3-4 hours. Depending
on when I get home.
On Aug 13, 2015 2:13 PM, "Vinicius Juvinski" <notifications@github.com>
wrote:

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

earsneyes, 2015-08-13:
there were something reported about Emax 12A esc's incompatibility at least in combination with Pixhawk i think. search diydrones or drone-discuss.
there is a hardware fix as well (removing a smd component).

awright424, 2015-08-13:
I have looked through the diy drones and only see mention of the 4 in 1 esc nothing concrete stating issues with the 12a simonk esc's. I was also wondering if I need to be using a H quad setup with the emax 250 nighthawk or if I should be using the X quad frame?

juvinski, 2015-08-13:
I have this 12A on a 250 tricopter and one thing for me, I always need to calibrate the esc's at least 2  times to work ok - on first time always one motor or starts after all others or the speed are different.

awright424, 2015-08-13:
i noticed at times all 3 motors start and one twitches a bit before spinning. So I dont know if its loose connections right now or not. I will inspect each connection and see what happens.

El-Mango, 2015-08-13:
What about propellers spinning direction? Did you check?
Just in case...
-e

awright424, 2015-08-13:
I believe I have things set up properly. I will make a video showing how
things are. I am still unsure if I should be running h or x quad setup.
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

mirkix, 2015-08-13:
Hi Alex,
please also provide the log files which you can find here on your bbb: `/var/APM/logs/`. I had some successful flights today with Stab, Auto and RTL.
Best regards
Mirko

awright424, 2015-08-14:
I woke up and started messing around and realized that I have a revision 1.0 pcb. Are the motor labels correct? Where in ardupilot itself can I see where the motors should be hooked up to what output? I will attach some pictures to this thread.

awright424, 2015-08-14:
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

earsneyes, 2015-08-14:
that should be the problem. The first pcbs had the order wrong. Revision 1.2 and fixed that.
https://github.com/mirkix/BBBMINI-PCB/blob/master/picture/bbbmini.png
I would try to connect them to the servo connector row on the back side if cable length is enough.

awright424, 2015-08-14:
I have and something still feels off to me. I will be testing the esc's etc
and will have a different flight controller to use in a week or so to test
with as well. I noticed that it seems to want to roll to the right in
stabilize and that pushing forward on the right stick, brain fart, makes it
want to fly backward. So I'm not sure if its the quad or possibly
transmitter doing something retarded
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

awright424, 2015-08-15:
any ideas guys? I'm at my wits end, only option i can see is ordering a cheap cc3d or something to test with to make sure wiring is good. If I cant wait for this pihat to come I may have to.

juvinski, 2015-08-16:
Hi,
In some cases, you need to invert the pitch channel - if in mission planner you move the stick forward and on mission planner you see the bar for pitch going up, so you need to invert the channel on the radio.
About roll, first - sorry to insist, but have you recalibrate the esc? Have you checked the gravity center ?How is the Balance props ? Vibrations ?
Have you tried trim this roll on transmitter? Was possible to fix ?

awright424, 2015-08-16:
so the issue seems to be the gyro. I got a new one but for some reason if I calibrate for instance and place it level it takes a while for it to actually show as being level in apm planner 2.0

I dont know what else to do. it got off the floor today almost a foot or so before immediately flying towards my front door. I chopped the throttle and looked at apm with it level and it showed it being off in apm. not sure if the barometer could be interfering. I received a replacement mpu9250 and have two more coming. I also have two ms5611's coming as well.

mirkix, 2015-08-16:
Hi Alex,
the best way to solve such a problem is to look into the log files, or provide them to us.

They are located here: `/var/APM/logs`

awright424, 2015-08-16:
https://drive.google.com/file/d/0B4rh1bWqHxtLaXR3dnVTdTkzMWc/view?usp=sharing

here is the latest log file should include the crash as well. not sure why i am getting the behaviour i am from two different gyros. Ive broken two sets of props and am getting frustrated now.

mirkix, 2015-08-16:
Hi Alex,
you can load the log file with APM Planner and look into it. You can see that there are two pulse with throttle input (and output to the esc s). But there is no change in pitch or roll at that time. At the end, when pitch and roll changed, there is no throttle input, maybe because you are lifting the quad up. Maybe it is the wrong log, can you check that?

awright424, 2015-08-16:
https://drive.google.com/file/d/0B4rh1bWqHxtLMl81SjFpZ01tdDA/view?usp=sharing
https://drive.google.com/file/d/0B4rh1bWqHxtLd3BUTHN2eEN5a2s/view?usp=sharing

here are my most recent logs. the latest should show me getting off the ground for a second or two. i smiled. lol

awright424, 2015-08-16:
Oh and in regards to your earlier question I do not remember lifting it if only at the end. Last two logs should have no lifts included

juvinski, 2015-08-17:
Hi Alex,

I'm look your logs and - at least for me, the first and strange thing is you are having something strange with Vibrations - there is just AccZ measurement and is out for regular value - yours are between a and 3.1 instead -15 to -5.
Other strange thing is you just have desired roll and pitch not the current measurement.
How is the value you have in your Log Bitmask ?

awright424, 2015-08-17:
The beaglebone black may not be mounted securely enough to the quad? Or
does it need to be on vibration dampers? What is this bitmask value you
speak of
On Aug 17, 2015 12:39 PM, "Vinicius Juvinski" <notifications@github.com>
wrote:

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

juvinski, 2015-08-17:
Hi Alex,
this can help about Log Bitmask(http://copter.ardupilot.com/wiki/common-downloading-and-analyzing-data-logs-in-mission-planner/) - I recommend for now enable almost all :)
About Vibrations is extremely hard to analyze but first, there are something strange because you don't have in your logs nothing about roll and pitch and your yaw are with strange values.
Running the tests are everything fine with all sensors ?

awright424, 2015-08-20:
Mirkix,
 I was wondering if the 1.0 board could have anything to do with the issues I have been dealing with? I should be getting the barometers delivered by this weekend as well as some pins etc. Then I would be able to try out a new board to see if the issue was caused by something I'm not seeing.

awright424, 2015-08-20:
So I got my mpu9250 in the mail today. I should have the pins I need coming in to be able to solder up the other 1.0 board I have. Mirkix do you have anymore of the current pcb's? I need to send you some money through paypal if that is the case. I tried out my motors and esc's with a cc3d atom and it flies fine. With that being said I have bought a pixhawk anti-vibration mount as I had the board mounted directly to the frame of the quadcopter. Can you guys show how you have mounted your own beaglebone blacks to a quadcopter frame? I think I may try to design a 3d printed quadcopter frame that integrates mounts for the beaglebone and access holes etc for certain ports.

mirkix, 2015-08-20:
Hi Alex,
you can use Rev 1.0 boards, but be sure you use the right RC_Out to ESC configuration. I saw at your last logs that you fly in acro mode, please make sure to start in stab mode for the first flights. Be sure to mount the breakout boards tight (see picture) to prevent vibration.
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
I do not have a Rev 1.4 board at the moment. You can look here, to order a small amount by yourself https://github.com/mirkix/BBBMINI-PCB#pcb.

awright424, 2015-08-20:
how do you have the beaglebone black mounted then? I did not have supports on the outside of the mpu9250 and ms5611 so that may be causing the issues you guys noticed.

mirkix, 2015-08-20:
The BeagleBone Black is hard mounted to the quadframe with nylon spacer, like the mpu9250 and ms5611. Before your next flight, you may disassemble the probs and "listen" to the motors when you arm you copter in stab mode and move the sticks or the copter. The sound must make sense, also take a look to the log or "real" time telemetry in apm-planner.  When all seems ok, mount the probs and try a real flight.

awright424, 2015-08-25:
turns out i have a bad esc which is more than likely the culprit for my issues. I also have been getting unhealthy compass errors. So I have the parts to solder up a new board so I will go ahead and get one going.

awright424, 2015-08-30:
my beaglebone is flying. I no longer have any issues. I have one question. how do you guys start arducopter/plane/etc on boot?

awright424, 2015-08-30:
I also seem to have to constantly calibrate the compass due to it not being healthy. This is very annoying as it means there is no quick way for me to get flying.

earsneyes, 2015-08-30:
I've put a line into my /etc/rc.local to start the rover in a screen session like this:

(sleep 10 && /usr/bin/screen -dmS rover /root/APMrover2.elf -A udp:192.168.1.37:14550 -B /dev/ttyO5 -C /dev/ttyUSB0)

You might need to install screen first:

`sudo apt-get update && sudo apt-get install screen`.

-A is my gcs udp connection, -B is the GPS module and -C is an 3DR radio connected to the USB-port.

Using two telemetry outputs only works when the ethernet cable is connected as far i can tell.
So im powering up my rover while wired to my home LAN and then head out to my test track, will add a wifi dongle instead of the cable soon.

Closed 2015-08-31.

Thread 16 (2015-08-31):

compass needs to be recalibrated all the time

awright424, 2015-08-31:
I am not sure why i have to calibrate my compass every time i try to fly and half the time i cant get it to work properly. Is the resistor on the board for the compass? or is that for the canbus items? I am just not sure why i am forced to constantly re-calibrate the compass when i want to fly. BTW when it is calibrated it flies well. I need to do some tuning and get some fpv going with an android application. But after looking at how far I was able to get it I am wondering how to handle long range wifi.

earsneyes, 2015-08-31:
Not sure why you need to recalibrate each time. You are using a external compass i guess ?
For the range i will be using a patch antenna and a wifi router.

awright424, 2015-08-31:
examples of antenna and type of router? And no I am not using an external compass the one that is on the board itself.

juvinski, 2015-08-31:
Hi Alex,

It's possible interference?
Have you testes the board off the quad ?

awright424, 2015-08-31:
this is with the beaglebone black being powered through a 5v adapter as well. I am wondering if I need to try to compensate for the motors or anything.

earsneyes, 2015-08-31:
Im using a Fonera router with dd-wrt and a supplied antenna. They are not manufactured/sold anymore i think.

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

awright424, 2015-08-31:
what would you be using on the quad?

earsneyes, 2015-09-01:
I have a TP-LINK TL-WN727N wifi dongle but can not recommend it because it was little bit of a pain to get it working.

Closed 2015-09-10.

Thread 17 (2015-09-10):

gps

awright424, 2015-09-10:
so I have this gps, https://goo.gl/photos/A2TdszUf7XFuapvy7, how do you recommend I connect it to the cape? Will there be any revisions that will support standard connections?

mirkix, 2015-10-30:
@awright424 You have to connect the GPS RX to the BBBMINI TX and the GPS TX to the BBBMINI RX. Also GND has to be connected to GND. Make sure the GPS TX is a 3.3 Volt signal. 2.54mm pin header are the BBBMINI standard connections :-)

Closed 2015-10-30.

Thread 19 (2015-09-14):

Compass issues

awright424, 2015-09-14:
I am constantly plagued with issues related to the compass. I have tried calibrating my compass for the last 3 days. I get errors with compass variance and am unable to arm because of this.I have a new zmr250 carbon fiber frame with pdb. I thought initially it was the carbon fiber on the top plate causing issues but it didn't change things with it removed. I have this issue with two 1.0 boards I have

Closed 2015-10-27.

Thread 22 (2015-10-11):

can you chenge aiopru pwm to 300hz or higt

cudnn, 2015-10-11:
i see PWM_FREQ_DEFAULT is 50 hz ，may i chenge it to 300 or 400 and so on.

but i see  it no possobal.can you re write the aiopru.

mirkix, 2015-10-11:
@cudnn Why it is not possible? You can change the frequency in user space with `set_freq` (https://github.com/diydrones/ardupilot/blob/master/libraries/AP_HAL_Linux/RCOutput_AioPRU.cpp#L67)

Closed 2015-10-30.

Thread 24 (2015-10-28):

Unstable flipping bbbmini

El-Mango, 2015-10-28:
Hi all,

I have a problem with an unstable bbbmini quad. Flipping upside-down both starting from ground or launching by hand.

### The hardware configuration is:
* Frame - Tarot TL300A
* Motor - MultiStar 2206 Baby Beast
* Prop - 5040 Multirotor ABS
* ESC - Afro 12A OPTO V3
* Flight Control - BBB + bbbmini
* Battery - Turnigy nano-tech 1300mAh 3S 45
* UBEC - HKU5 5V/5A
* RX Receiver - X8 R6M 6Ch Micro 2.4GHz Assan
* TX Transmitter - JR BX8103A

### About software:
I followed exactly the steps list on the website (https://github.com/mirkix/BBBMINI/blob/master/doc/software/software.md)
both, compiling and downloading the 3.3 ArduCopter.elf version.
(from http://firmware.bbbmini.com/ArduCopter.elf)

More or less I've got the same results: No way to fly the copter !

Please notice that I had to modify the parameters, due to my TX:
* RCMAP_PITCH         = 3
* RCMAP_ROLL          = 2
* RCMAP_THROTTLE = 1
* RCMAP_YAW           = 4

The sensations, holding the copter in stabilized mode hanging from my hand, are:

1. Pitch and Roll were exchanged (acting Pitch on the transmitter, made Roll action on drone) even if the representation on the Radio Calibration screen is correct after RCMAP (Pitch with Pitch etc...)

2. Not using transmitter (just mid throttle), stabilizer reaction to manual solicitation was not correct (not equal and contrary to the cause, to keep it stable).

My supposition is that motors are acting in wrong order...
But they are correctly connected !!! No way to go wrong on BBBMINI Printed Board. (They all push up!)

Maybe RC-IN reader piece of code, RCInput_AioPRU.cpp, doesn't handle RCMAP channel substitution ?
Or something else down the line of signal management and motor control?

I'm suspecting of RCMAP because it's the only modification that I made, comparing with standard procedure...
Am I the only one who is trying to use RCMAP channels substitution with bbbmini? (I really cannot change channel number in the TX, only reverse)

What do you thing? Any idea?

Thanks and bye,
Enrico.

earsneyes, 2015-10-28:
Hi Enrico, can you add a picture of your quad maybe ?

El-Mango, 2015-10-28:
Sure I can...
-e
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

earsneyes, 2015-10-28:
Thanks Enrico, i think it could be vibration maybe.
Small copters tend to have strong vibrations so i would look at this as well to see if it is in the acceptable range.

[http://copter.ardupilot.com/wiki/common-measuring-vibration/](http://copter.ardupilot.com/wiki/common-measuring-vibration/)

I use [Gel pads](http://copter.ardupilot.com/wiki/common-vibration-damping/#gel_pads) and it works pretty well.

mirkix, 2015-10-28:
@El-Mango Hi Enrico, can you check that the upper left motor is connected to RC_2. It seems so, that the motor is connected to RC_1.

earsneyes, 2015-10-28:
@mirkix good catch!

El-Mango, 2015-10-28:
UPS !!!!!
:-|

Closed 2015-10-28.

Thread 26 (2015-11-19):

Use 4.1 kernel with capemgr

jadonk, 2015-11-19:
Rather than using a replacement .dtb, I recommend using a .dtbo and using the 4.1 kernel. You can use the /opt/scripts/tools/update_kernel.sh script that is on the image (https://github.com/RobertCNelson/boot-scripts/blob/master/tools/update_kernel.sh).

See http://elinux.org/Beagleboard:BeagleBoneBlack_Debian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 for the flags to pass /opt/scripts/tools/update_kernel.sh.

I used:

    sudo apt-get update
    sudo apt-get install -y lsb-release
    sudo /opt/scripts/tools/update_kernel.sh --ti-rt-channel --testing

I just used a newer console flasher, rather than doing 'sudo apt-get upgrade'. I find using 'sudo apt-get upgrade' removes the usefulness of telling people to grab a particular image because it is unpredictable what might break. Doing the 'update_kernel.sh' script, rather than specifying a version, also adds some unpredictability, but at least I know that is coming from the BeagleBoard.org community, rather than Debian at large.

jadonk, 2015-11-19:
My reference process that I'm documenting as I go: https://gist.github.com/jadonk/ef22de2d04e93022d623

mirkix, 2015-11-19:
@jadonk Hi Jason,
I am using 4.1 already, but before 4.1.13 ti rt r31 released yesterday, CONFIG_SPI_DEBUG=y was enabled and blowing up your log files when ardupilot is running. I am in contact with Robert and there is a DTB file for 4.1 https://github.com/RobertCNelson/dtb-rebuilder/blob/4.1-ti/src/arm/am335x-boneblack-bbbmini.dts available. I will switch to 4.1 on BBBMINI GitHub after the first successful flight.
I think change to `update_kernel.sh` is a good idea.

mirkix, 2015-12-18:
@jadonk
We are now using `update_kernel.sh`and Kernel 4.1.

Closed 2015-12-18.

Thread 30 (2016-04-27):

Fresh installation RCOutput issue

aaraujo11, 2016-04-27:
Hi, i have done a fresh installation following the all the steps in software section, but when i'm try to run a simple test (RCOutput.elf) to check the output to the motors, but sometimes the motors start to spin, and other times they simple start to beep more fast, without spin the motors. When i run the main routine (arducopter-hexa) the behavior is the same just beeping. It seems to be a problem in the pwm signal or the pru that isn't active. His there any test to check what is the issue?

In using a hexacopter, with the bbbmini pcb rev.1.4, and DJI 2212 930kv motors and the E300 ESC's.

juvinski, 2016-04-27:
HI Andre,

have you calibrate the radio ?

mirkix, 2016-04-27:
Hi Andre,

do you use Kernel 4.4? `uname -a`

aaraujo11, 2016-04-27:
Hi @mirkix, the kernel version is
Linux beaglebone 4.4.8-bone-rt-r10 #1 PREEMPT RT Fri Apr 22 04:15:41 UTC 2016 armv7l GNU/Linux

@juvinski do you mean to calibrate the esc's? By set the max and the min os the pwm values?

mirkix, 2016-04-27:
RCOutput.elf is sweeping the PWM value. Some ESCs need a low PWM value for some time because of security reason. RCOutput.elf could be used to test servos but you can get trouble when you use it with ESCs.
I have to check this Kernel on my system.

aaraujo11, 2016-04-27:
I have it working with the version of December/January. Meanwhile i need to use the BB all this months to other things and i had to flash it. Now that i have some available time, i want to put the hexa flying again.

juvinski, 2016-04-27:
Hi Andre,

Yes, i had problems with some escs beeping until I set the values.

mirkix, 2016-04-27:
Can you try Kernel 4.1 `sudo /opt/scripts/tools/update_kernel.sh --bone-rt-kernel --lts-4_1` and reboot if this helps.

aaraujo11, 2016-04-27:
@mirkix apparently after downgrade the kernel to the 4.1 the RCOutput test work fine, but as @juvinski refer i have to calibrate the radio to define the min and max values, to stop beeping after launch the main routine (arducopter-hexa). I will done some tests before close this issue. Anyway thanks guys for the support! Cheers!

mirkix, 2016-04-28:
@aaraujo11 Checked with Kernel 4.4 without issues here.

aaraujo11, 2016-04-28:
Hi @mirkix, yes i upgrade again to the kernel 4.4, and it is working! Probably as sometimes it works and other times doesn't, i wrongly assume that it has a problem with the kernel, but never thought it will a problem of radio calibration, once the RCOutput test routine supposedly sweeps all ranges of values. But the realty is that with kernel 4.1 RCOutput test routine works, without doing any radio calibration. Anyway thanks for the support!

Just a few questions:

1) For the acc calibration, once in the APM planner, it always give a timeout, a possible way to set the offsets, is run the INS_generic.elf, and calibrate it and get the offset values and insert it directly in APM planner params list, is it the correct way to do it?

2)  What do you use for communicate with or BB? Have your create a wifi access point? Or do use a serial bluetooth module? I have read some comments that using wifi isn't ideal because it may interfere with radio receiver, since they operate in the same frequency 2.4GHz (if you aren't use the new 5GHz), have you experience any interference?

3) I notice in one of your youtube videos you have a status display, in your quad, is there the code available in ardupilot community, or have you develop it?

juvinski, 2016-04-28:
Hi Andre,
I think some questions I can answer.
The Oled display is available at ardupilot main respository and uses a I2C oled  display - it's cool and enabled by default.
About connection, I'm always using 3dr compatible telemetry module - frequency is 915 Mhz as main interface connection. I tried wifi with ad hoc support and works fine too. Regarding interference, is always a risk.

aaraujo11, 2016-04-28:
Hi Vinicius, it is really useful the display info the get the status, i have one oled module of that i will try it! Regarding the connection once i don't have a telemetry module, i will try to config a wifi AP. Thanks!

Closed 2016-05-02.

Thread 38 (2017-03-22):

pru firmware

awright424, 2017-03-22:
Used the latest beaglebone black image and grabbing arducopter and compiling on debian leaves me with this error when attempting to start ardupilot. I have verified as well that the dtb is being loaded initially.

this is what i see in dmesg

`[ 2104.096701] Unhandled fault: external abort on non-linefetch (0x1818) at 0xb6fe2000
[ 2104.096707] pgd = dc308000
[ 2104.096717] [b6fe2000] *pgd=9c354831, *pte=4a324343, *ppte=4a324833
[ 2112.307359] Unhandled fault: external abort on non-linefetch (0x1818) at 0xb6fd6000
[ 2112.307365] pgd = dcd38000
[ 2112.307376] [b6fd6000] *pgd=9c451831, *pte=4a324343, *ppte=4a324833
[ 2116.818783] Unhandled fault: external abort on non-linefetch (0x1818) at 0xb6fe8000
[ 2116.818789] pgd = dcf40000
[ 2116.818799] [b6fe8000] *pgd=9cd64831, *pte=4a324343, *ppte=4a324833
[ 2530.019735] Unhandled fault: external abort on non-linefetch (0x1818) at 0xb6f80000
[ 2530.019740] pgd = ddc64000
[ 2530.019751] [b6f80000] *pgd=9c406831, *pte=4a324343, *ppte=4a324833`

 RCOutputAioPRU.cpp:SIGBUS error gernerated

awright424, 2017-03-23:
using the image mentioned in software works. so it appears the pru firmware is not available or needs to be built and installed on the newest image i would assume.

awright424, 2017-04-06:
Can you provide instructions on where the pru firmware needs to be etc? Is it just compiling said pru firmware and copying to /lib/firmware? I would like to use newer images and not be forced to have to use the image specified in the instructions.

juvinski, 2017-04-06:
Hi,

The dtb are been charged at boot time ?

awright424, 2017-04-06:
If I use the iot debian image and install realtime kernel etc its fine. but it doesnt appear that the pru firmware is loaded. I have not confirmed the  bbbmini dtb is loaded but it has been added using the sed command you provided. I figured I would be able to build the pru firmware and install it myself.

mirkix, 2017-04-15:
@awright424 BeagleBone Blue is running the IoT image and the firmware in running fine.

awright424, 2017-04-15:
Is the beaglebone black still using a bbbmini specific dtb and pru as I
believe I saw a blue specific dtb and pru. Even so for those who would like
to use other distros, arch Linux etc it would be great to have better
instructions as to where the pru firmware built would need to reside.

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

awright424, 2017-04-22:
`[alex@archlinux ~]$ ssh debian@192.168.0.8
Debian GNU/Linux 8

BeagleBoard.org Debian Image 2017-03-19

Support/FAQ: http://elinux.org/Beagleboard:BeagleBoneBlack_Debian

default username:password is [debian:temppwd]

The programs included with the Debian GNU/Linux system are free software;
the exact distribution terms for each program are described in the
individual files in /usr/share/doc/*/copyright.

Debian GNU/Linux comes with ABSOLUTELY NO WARRANTY, to the extent
permitted by applicable law.
Last login: Sat Apr 22 15:22:22 2017 from 192.168.0.5
debian@beaglebone:~$ ls
arducopter-quad  bin
debian@beaglebone:~$ sudo ./arducopter-quad
[sudo] password for debian:
RCOutputAioPRU.cpp:SIGBUS error gernerated

debian@beaglebone:~$
`

this doesnt appear to be the case. I have even mentioned the need for instructions for manually compiling and installing the pru firmware. I know it should be more than just enabling the bbbmini dtb. this is the latest bone-debian-8.7-iot-armhf-2017-03-19-4gb.img

This really causing me alot of headaches as I would like to use other distributions on beaglebone black with bbbmini.

mirkix, 2017-04-23:
@awright424 try to remove / delete `/etc/modprobe.d/pruss-blacklist.conf`

jackcarrozzo, 2018-07-10:
I'm having this problem too, followed all the directions as best I can and still can't figure out what I missed. I don't have an /etc/modprobe.d/pruss-blacklist.conf

How can I confirm if my PRU DTB is loading?

awright424, 2018-07-10:
Check your uEnv.txt file located in boot. That loads the correct dtb that
was my issue with pocketpilot a day ago.

On Tue, Jul 10, 2018, 12:12 PM Jack Carrozzo <notifications@github.com>
wrote:

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

jackcarrozzo, 2018-07-10:
Per instructions I have in my uEnv.txt:

`uname_r=4.9.105-ti-rt-r113
dtb=am335x-boneblue.dtb
uboot_overlay_pru=/lib/firmware/AM335X-PRU-RPROC-4-9-TI-00A0.dtbo`

I can confirm also that /lib/firmware/AM335X-PRU-RPROC-4-9-TI-00A0.dtbo exists.

Appreciate any other leads you can give me!

awright424, 2018-07-10:
uname_r=4.9.88-ti-rt-r111
enable_uboot_overlays=1
uboot_overlay_pru=/lib/firmware/AM335X-PRU-UIO-00A0.dtbo
enable_uboot_cape_universal=1
cmdline=coherent_pool=1M net.ifnames=0 quiet

your uEnv.txt needs to be something like this. You have the wrong dtbo being loaded.

jackcarrozzo, 2018-07-10:
I get the same error using /lib/firmware/AM335X-PRU-UIO-00A0.dtbo, unfortunately.

Closed 2017-05-03.

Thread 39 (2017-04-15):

Handling Interrupt

AmirhosseinR, 2017-04-15:
Hello Denecke;
Thanks for sharing your interesting project. I have one question about Linux embedded programming. How do you handle hard interrupt? For Example external interrupt that comes from MPU-9250:
1- By Polling GPIO in Linux user space (c code and thread)
2- By using PRU (poll GPIO and send soft interrupt to Linux USER SPACE)
3- Linux Kernel Programming (Which support hard interrupt)
Or we can do it in RT-Linux by programing USER SPACE
Yours Sincerely,
Rostami;

mirkix, 2017-04-15:
@AmirhosseinR I can't help here. BBBmini does not use the INT pin yet.

Closed 2017-04-15.

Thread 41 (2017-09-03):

SPI unable to open

OscarJGV26, 2017-09-03:
Hi,

I am trying to run it in the Beaglebone Blue... I tried using the image provided in (https://github.com/mirkix/ardupilotblue) and at first it ran correctly but then it gave an error of No INS backend available.

I am having the following error

root@beaglebone:/home/debian# /home/debian/arducopter -C udp:192.168.137.1:14550
SPI: unable to open SPI bus /dev/spidev2.1: No such file or directory

I checked the /dev folder and spidev2.1 is not there,
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

I would assume is just a matter of changing it but I am thinking maybe I missed something. I ran all the steps in (https://github.com/mirkix/BBBMINI/blob/master/doc/software/software.md).

Any suggestions?

Regards,
Oscar

patrickpoirier51, 2017-09-04:
Looks like you do not have the correct binary... this one is looking for SPI connected sensors that are on the BBBMINI not on the BBBlue
You should use gitter for these type of question: https://gitter.im/mirkix/BBBMINI
Regards

OscarJGV26, 2017-09-04:
Hi patrick,

Yes. This was my bad. I followed the suggestions in ([1]https://github.com/mirkix/BBBMINI/blob/master/doc/software/software.md) to the letter but they are for BBBMINI as you suggested.

I corrected this by avoiding step 16 in [1] and selecting board=blue in step [4] of compiling.

I got confused because this process is not described in ([2] https://github.com/mirkix/ardupilotblue) since it provides the image but I wanted to build it for my self.

As for the No INS backend, I don't know what was exactly but when I ran all the steps in [2] then all the compiling steps in [1], it worked.

Regards,
Oscar

juvinski, 2017-09-04:
hi @OscarJGV26 ,

BBBMini use spi for 9DOF sensor while BBBBlue use just i2c for both 9DOF and Baro, that is the reason you are having this troubles.

OscarJGV26, 2017-09-04:
hi Juvinski,

Yes. I realized I made that mistake on selecting board=blue and also, I assume, loading wrong cape layout in step 16.

Thank you very much.

Closed 2018-01-04.

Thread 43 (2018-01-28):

Request to provide the libraries being used

Thalaivar, 2018-01-28:
This was such a lovely project and I built one of these myself! I request you to tell me which libraries you used and provide me any that you wrote yourself for the sensors, RC, UART etc. I have been hunting everywhere for them and I have only found your PRU firmware on hackster.io

mirkix, 2018-02-11:
All libraries are part of ArduPilot, you can take a look at https://github.com/ArduPilot/ardupilot .

Regards
Mirko

Closed 2018-02-11.

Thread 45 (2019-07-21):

libm.so.6: version `GLIBC_2.27' not found

HomeLH, 2019-07-21:
`./ardusub: /lib/arm-linux-gnueabihf/libm.so.6: version `GLIBC_2.27' not found (required by ./ardusub)
`
Crosscompile master computer runs on Ubuntu 18.04.

mirkix, 2019-07-21:
@HomeLH Hi, yes that is an issue because Ubuntu 18.04 is using an newer GLIBC. You can download http://releases.linaro.org/components/toolchain/binaries/4.9-2017.01/arm-linux-gnueabihf/gcc-linaro-4.9.4-2017.01-i686_arm-linux-gnueabihf.tar.xz and put the bin folder in your PATH before the Ubuntu arm compiler. With taht you should be able to compile ArduPilot with Ubuntnu 18.04 for BBBmini. I will check that and but in in the doc.

HomeLH, 2019-07-27:
@mirkix Thanks very much. It does work well, the detailed log:
`hogan@hogan-ThinkPad-T480:~/ardupilot$ ./waf configure --board=bbbmini
Setting top to                           : /home/hogan/ardupilot
Setting out to                           : /home/hogan/ardupilot/build
Autoconfiguration                        : enabled
Setting board to                         : bbbmini
Checking for program 'arm-linux-gnueabihf-ar' : /opt/gcc-linaro-4.9.4-2017.01-i686_arm-linux-gnueabihf/bin/arm-linux-gnueabihf-ar
Using toolchain                               : arm-linux-gnueabihf
Checking for 'g++' (C++ compiler)             : /opt/gcc-linaro-4.9.4-2017.01-i686_arm-linux-gnueabihf/bin/arm-linux-gnueabihf-g++
Checking for 'gcc' (C compiler)               : /opt/gcc-linaro-4.9.4-2017.01-i686_arm-linux-gnueabihf/bin/arm-linux-gnueabihf-gcc
Checking for program 'arm-linux-gnueabihf-pkg-config' : /usr/bin/arm-linux-gnueabihf-pkg-config
Checking for need to link with librt                  : not necessary
Checking for 'lttng-ust'                              : not found
Testing link with lttng-ust                           : yes
Checking for library dl                               : yes
Checking for 'libiio'                                 : not found
Testing link with libiio                              : yes
Checking for HAVE_CMATH_ISFINITE                      : yes
Checking for HAVE_CMATH_ISINF                         : yes
Checking for HAVE_CMATH_ISNAN                         : yes
Checking for NEED_CMATH_ISFINITE_STD_NAMESPACE        : yes
Checking for NEED_CMATH_ISINF_STD_NAMESPACE           : no
Checking for NEED_CMATH_ISNAN_STD_NAMESPACE           : no
Checking for header endian.h                          : yes
Checking for header byteswap.h                        : yes
Checking for program 'python'                         : /usr/bin/python
Checking for python version >= 2.7.0                  : 2.7.15
Checking for program 'python'                         : /usr/bin/python
Checking for python version >= 2.7.0                  : 2.7.15
Source is git repository                              : yes
Update submodules                                     : yes
Checking for program 'git'                            : /usr/bin/git
Checking for program 'arm-linux-gnueabihf-size'       : /opt/gcc-linaro-4.9.4-2017.01-i686_arm-linux-gnueabihf/bin/arm-linux-gnueabihf-size
Benchmarks                                            : disabled
Unit tests                                            : enabled
'configure' finished successfully (1.014s)
...
[1151/1160] Linking build/bbbmini/lib/libAntennaTracker_libs.a
[1152/1160] Linking build/bbbmini/lib/libArduCopter_libs.a
[1153/1160] Linking build/bbbmini/lib/libArduPlane_libs.a
[1154/1160] Linking build/bbbmini/bin/ardurover
[1155/1160] Linking build/bbbmini/bin/antennatracker
[1156/1160] Linking build/bbbmini/bin/arducopter-heli
[1157/1160] Linking build/bbbmini/bin/arducopter
[1158/1160] Linking build/bbbmini/bin/arduplane
[1159/1160] Linking build/bbbmini/lib/libArduSub_libs.a
[1160/1160] Linking build/bbbmini/bin/ardusub
Waf: Leaving directory `/home/hogan/ardupilot/build/bbbmini'

BUILD SUMMARY
Build directory: /home/hogan/ardupilot/build/bbbmini
Target               Text    Data  BSS    Total
------------------------------------------------
bin/ardurover        653173  1176  30024  684373
bin/antennatracker   516238  1128  28772  546138
bin/arducopter       848401  1200  35680  885281
bin/arducopter-heli  823576  1200  35536  860312
bin/arduplane        858979  1196  36596  896771
bin/ardusub          707163  1192  31496  739851

Build commands will be stored in build/bbbmini/compile_commands.json
'build' finished successfully (1m43.532s)
Waf: Entering directory `/home/hogan/ardupilot/build/bbbmini'
Waf: Leaving directory `/home/hogan/ardupilot/build/bbbmini'

BUILD SUMMARY
Build directory: /home/hogan/ardupilot/build/bbbmini
Target       Text    Data  BSS    Total
----------------------------------------
bin/ardusub  707163  1192  31496  739851
bin/ardusub  707163  1192  31496  739851

Build commands will be stored in build/bbbmini/compile_commands.json
'sub' finished successfully (1.325s)
`

Yatin-Khurana, 2022-09-25:
can you please post binaries here?

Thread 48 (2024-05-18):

Problem with calibirating ESCs

supriosamanta, 2024-05-18:
Hi, great project. I am currently implementing this using a begalbone black, mounted with a cape. I have followed the instructions provided on the BBBmini github page to download, configure and build the kernel and also the arducopter firmware. I am using the 4.0.6 version. My ESCs are from readytosky 30A (https://robu.in/product/readytosky-30a-2-6s-esc/) used with a 3s lipo. Here is the problem I am facing, on calibirating the ESCs manually, using my sbus based receiver, I achieve a consistent speed of 5000rpm on all my motors when the transmitter throttle is set to 50%. My motors can spin upto 10000 rpm. When the ESCs are plugged back to the begalbone black cape, following the diagram on the github page, the motors spin with different rpms. The difference in the RPM is usually around 2000-3000, sometimes more than 4000 rpm. Can you point out potential issues that can be causing this? My calibration sequence is the one mentioned in the ardupilot website. I have tried manual, all at once and semi automatic sequence but nothing seems to solve the problem.

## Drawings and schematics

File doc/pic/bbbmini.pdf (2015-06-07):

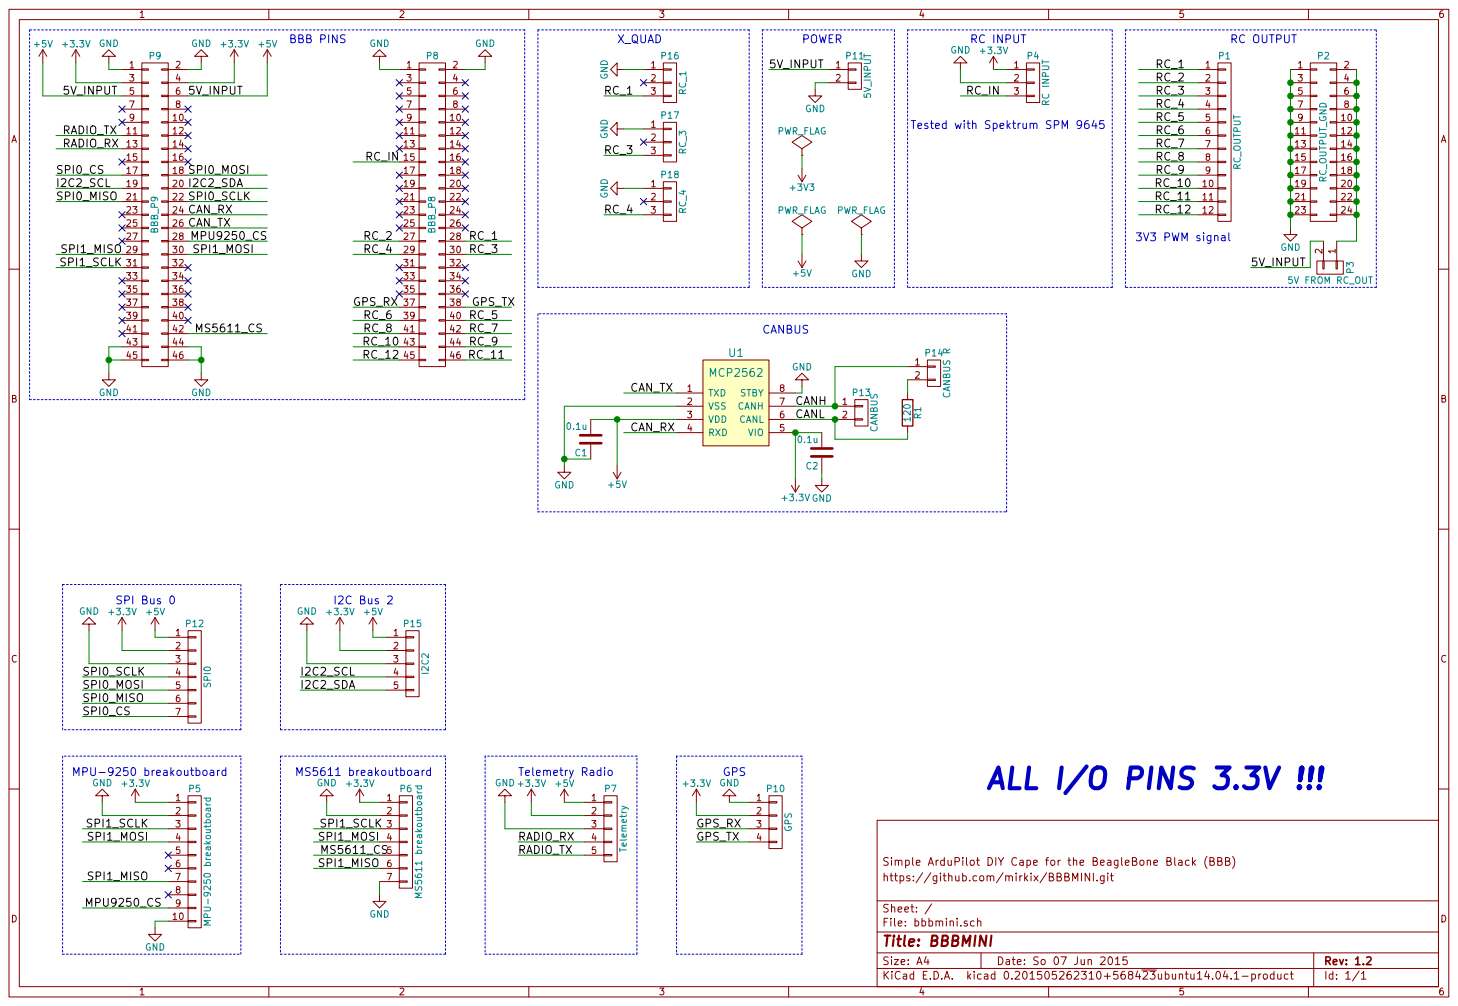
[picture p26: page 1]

Tested with Spektrum SPM 9645

Simple ArduPilot DIY Cape for the BeagleBone Black (BBB)
Id: 1/1 Title: BBBMINI File: bbbmini.sch Sheet: / https://github.com/mirkix/BBBMINI.git

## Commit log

2015-03-18 Update pin assigment
2015-03-20 Add UART4 MAVLink
2015-03-26 add CAN bus todo
2015-04-20 Add printed circuit board
2015-04-20 Add schematic
2015-04-20 Add power supply
2015-04-25 Add PS pin
2015-05-05 Add ADNS 3080 Optical Flow
2015-06-02 Correct power pins
2015-06-03 Add pcb and schematic
2015-06-03 Add pic and schematic
2015-06-03 add pcb pic
2015-06-07 PCB Rev 1.2
2015-06-08 Show PCB
2015-07-11 Add BBBMINI-PCB
2015-08-03 Add device-tree-compiler
2015-08-23 Adds a 3D printable case for protecting the bbbmini
    [bbbmini_1_4_case.stl, bbbmini_1_4_top_blank.stl, bbbmini_1_4_top_typo.stl]
2015-09-01 Move case files into case dir
    [bbbmini_1_4_case.stl, bbbmini_1_4_top_blank.stl, bbbmini_1_4_top_typo.stl]
2015-09-05 Add Device Tree
2015-09-10 A taller version of the Case for mounting the MPU-9250 and MS5611 breakout boards on to hex spacers / female header socket.
    [bbbmini_1_4_case_lifted.stl]
2015-09-15 Move case to BBBMINI-PCB
    [bbbmini_1_4_case.stl, bbbmini_1_4_case_lifted.stl, bbbmini_1_4_top_blank.stl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]
2016-02-08 Update to ADC dtbo
2016-02-17 change to ardupilot dir before submodule init
    Added one step for the install flow :)
2016-04-21 software: in jessie the device-tree-package has been patched for v4.1.x+ overlays
    users dont need to run ./dtc-overlay.sh anymore
2016-04-23 add esc pic
2017-03-26 Add links to boards
